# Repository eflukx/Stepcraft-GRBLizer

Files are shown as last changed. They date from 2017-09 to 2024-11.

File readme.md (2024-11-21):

# Stepcraft GRBLizer

A GRBL compatible controller for use as a drop-in replacement for the SC100 USB standard controller deliverd with Stepcraft CNC machines. This Arduino Uno compatible controller is wired conforming the GRL v0.9+ standard. The controller can be used with the GRBL firmware and with EstlCAM.

## Features
  - The PC is fully electrically isolated from the CNC machine (optional).
	- Device is powered via the Stepcraft machine (not from USB port) and optionally from the ISP port.
  - All inputs protected with clamping diodes and resistors.
  - Probe inputs have a 100 Ohm / 10nF low pass filter to suppress spurious triggering. (Filter values may be experimented with.)
  - 3.5mm Jack for spindle / laser / hot-end control
  - 3.5mm Jack input for 2 probes.
  - Serial interface fed out the back (TTL, not protected). For people in a hurry: CP2102 and isolator ICs can be left unpopulated.
  - Standard 6 pin ISP programming connector fed out the back  (not protected).
  - Some juper block for IO-config

Alvast een leuk plaatje:
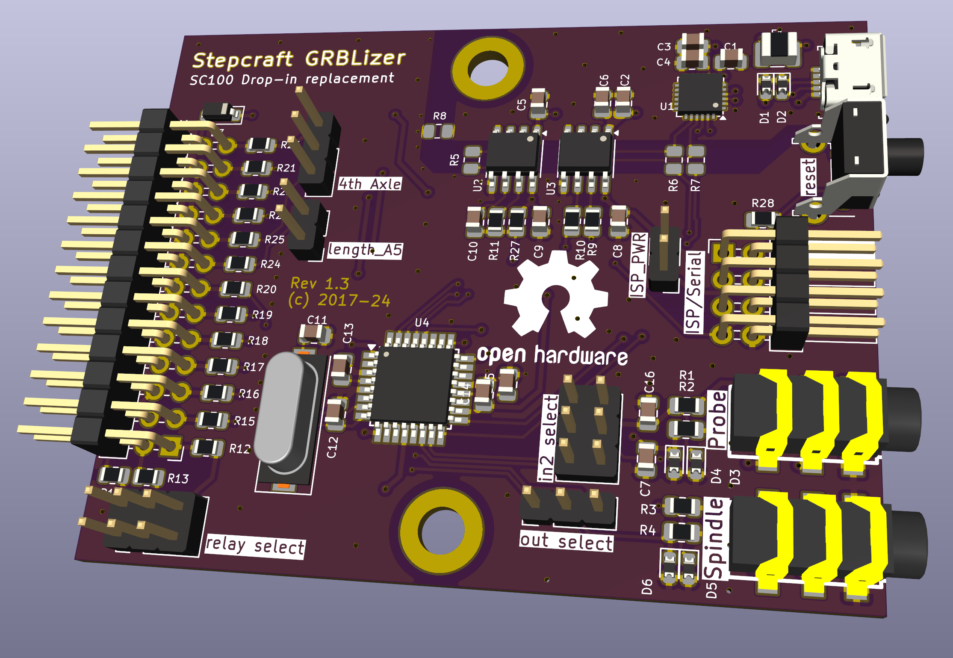
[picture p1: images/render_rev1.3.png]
PCB Render


# interactive BOM
Access the [interactive bom directly using this link](https://cdn.githubraw.com/eflukx/Stepcraft-GRBLizer/4cef8a3f/ibom/ibom.html)!
# Stepcraft 420 CNC settings with GRBLizer

Notes kindly provided by [Albin Stigö](https://github.com/ast) on getting [GRBL v1.1](https://github.com/gnea/grbl/wiki) working with the
[GRBLizer](https://github.com/eflukx/Stepcraft-GRBLizer) board.

Tested on Stepcraft 420, but probably works with most other Stepcraft types.

## Setup

* Stepcraft 420 CNC
* Stepcraft drivers with GRBLizer board
* [GRBL v1.1](https://github.com/gnea/grbl/wiki)
* [Universal-G-Code-Sender](https://github.com/winder/Universal-G-Code-Sender)

Install GRBL in the usual way. However you need to make some changes in config.h and cpu_map.h.

```c
/* cpu_map.h */

// The Stepcraft has all limits on one pin.
#define X_LIMIT_BIT    1  // Uno Digital Pin 9
#define Y_LIMIT_BIT    1  // Uno Digital Pin 9
#define Z_LIMIT_BIT    1  // Uno Digital Pin 9
```

```c
/* config.h */

// Since all limit switches end up being shared on one pin,
// we can only home one direction at a time.
#define HOMING_CYCLE_0 (1<<Z_AXIS)  // REQUIRED: First move Z to clear workspace.
#define HOMING_CYCLE_1 (1<<Y_AXIS)  // OPTIONAL: Then move X,Y at the same time.
#define HOMING_CYCLE_2 (1<<X_AXIS)  // OPTIONAL: Uncomment and add axes mask to enable

// The stop output of the Stepcraft board is inverted to what GRBL expects.
// However you simply can't swap the switch because the driver board will also
// disable the motors so nothing will move.
#define INVERT_CONTROL_PIN_MASK (1<<CONTROL_RESET_BIT) // Default disabled.
```

## GRBL settings

I haven't done a lot of fine tuning but these seems to work well enough.

```
$0 = 50				(Step pulse time, microseconds)
$1 = 100			(Step idle delay, milliseconds)
$2 = 0				(Step pulse invert, mask)
$3 = 0				(Step direction invert, mask)
$4 = 1				(Invert step enable pin, boolean)
$5 = 1				(Invert limit pins, boolean)
$6 = 0				(Invert probe pin, boolean)
$10 = 1				(Status report options, mask)
$11 = 0.010			(Junction deviation, millimeters)
$12 = 0.002			(Arc tolerance, millimeters)
$13 = 0				(Report in inches, boolean)
$20 = 0				(Soft limits enable, boolean)
$21 = 0				(Hard limits enable, boolean)
$22 = 1				(Homing cycle enable, boolean)
$23 = 1				(Homing direction invert, mask)
$24 = 120.000		(Homing locate feed rate, mm/min)
$25 = 900.000		(Homing search seek rate, mm/min)
$26 = 250			(Homing switch debounce delay, milliseconds)
$27 = 1.000			(Homing switch pull-off distance, millimeters)
$30 = 1000			(Maximum spindle speed, RPM)
$31 = 0				(Minimum spindle speed, RPM)
$32 = 0				(Laser-mode enable, boolean)
$100 = 133.333		(X-axis travel resolution, step/mm)
$101 = 133.333		(Y-axis travel resolution, step/mm)
$102 = 133.333		(Z-axis travel resolution, step/mm)
$110 = 800.000		(X-axis maximum rate, mm/min)
$111 = 800.000		(Y-axis maximum rate, mm/min)
$112 = 800.000		(Z-axis maximum rate, mm/min)
$120 = 10.000		(X-axis acceleration, mm/sec^2)
$121 = 10.000		(Y-axis acceleration, mm/sec^2)
$122 = 10.000		(Z-axis acceleration, mm/sec^2)
$130 = 300.000		(X-axis maximum travel, millimeters)
$131 = 420.000		(Y-axis maximum travel, millimeters)
$132 = 140.000		(Z-axis maximum travel, millimeters)
```

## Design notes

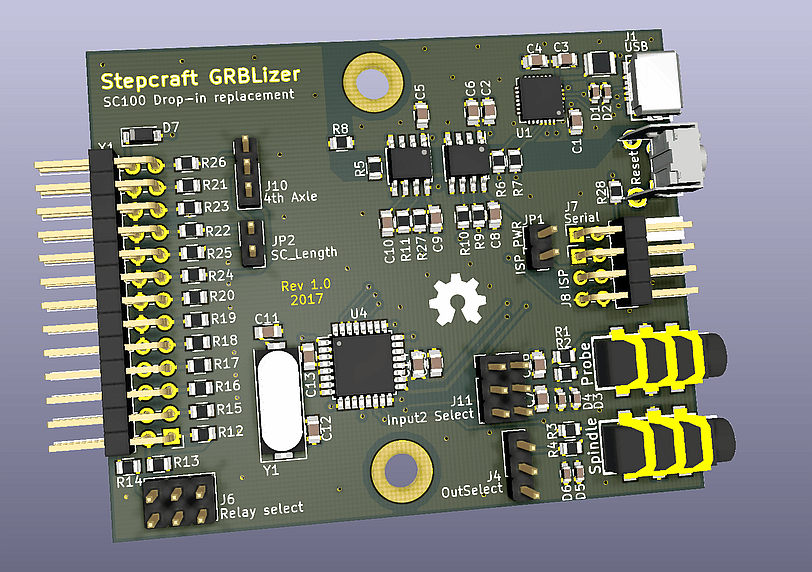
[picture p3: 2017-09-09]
images/render2_composit_web.png

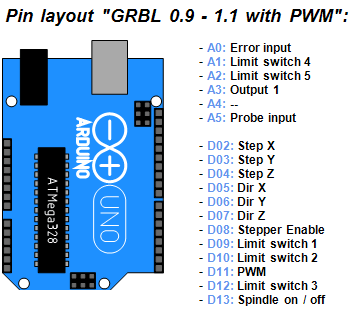
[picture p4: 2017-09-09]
images/GRBL_0.9+_PWM.png

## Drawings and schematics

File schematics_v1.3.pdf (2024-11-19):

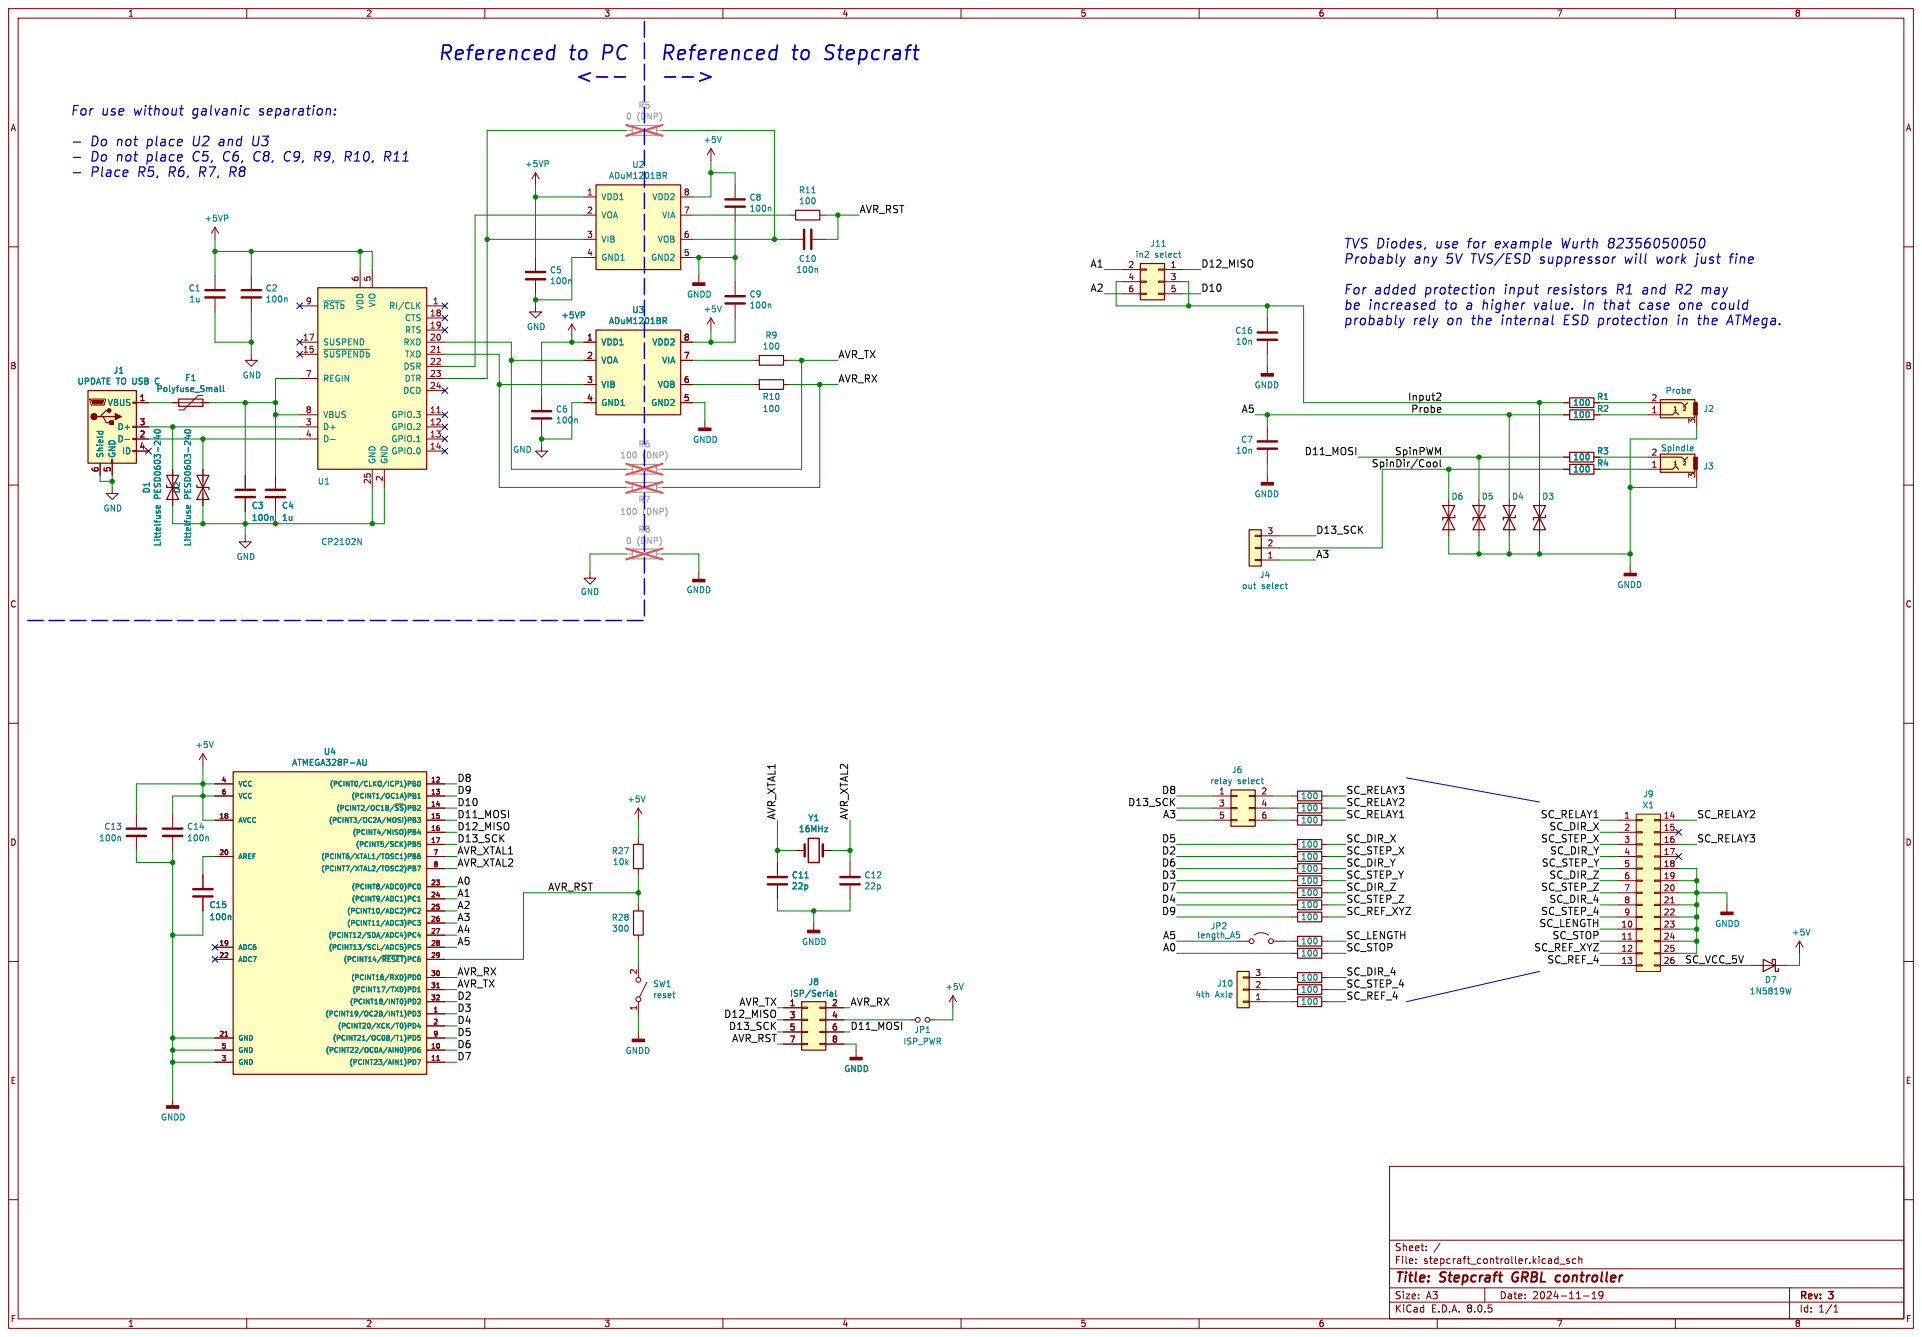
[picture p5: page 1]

TVS Diodes, use for example Wurth 82356050050

be increased to a higher value. In that case one could

2 RXD 20 TXD 21 DSR 22 DTR 23 DCD 24 GND 25 D+ 3 D- 4 VIO

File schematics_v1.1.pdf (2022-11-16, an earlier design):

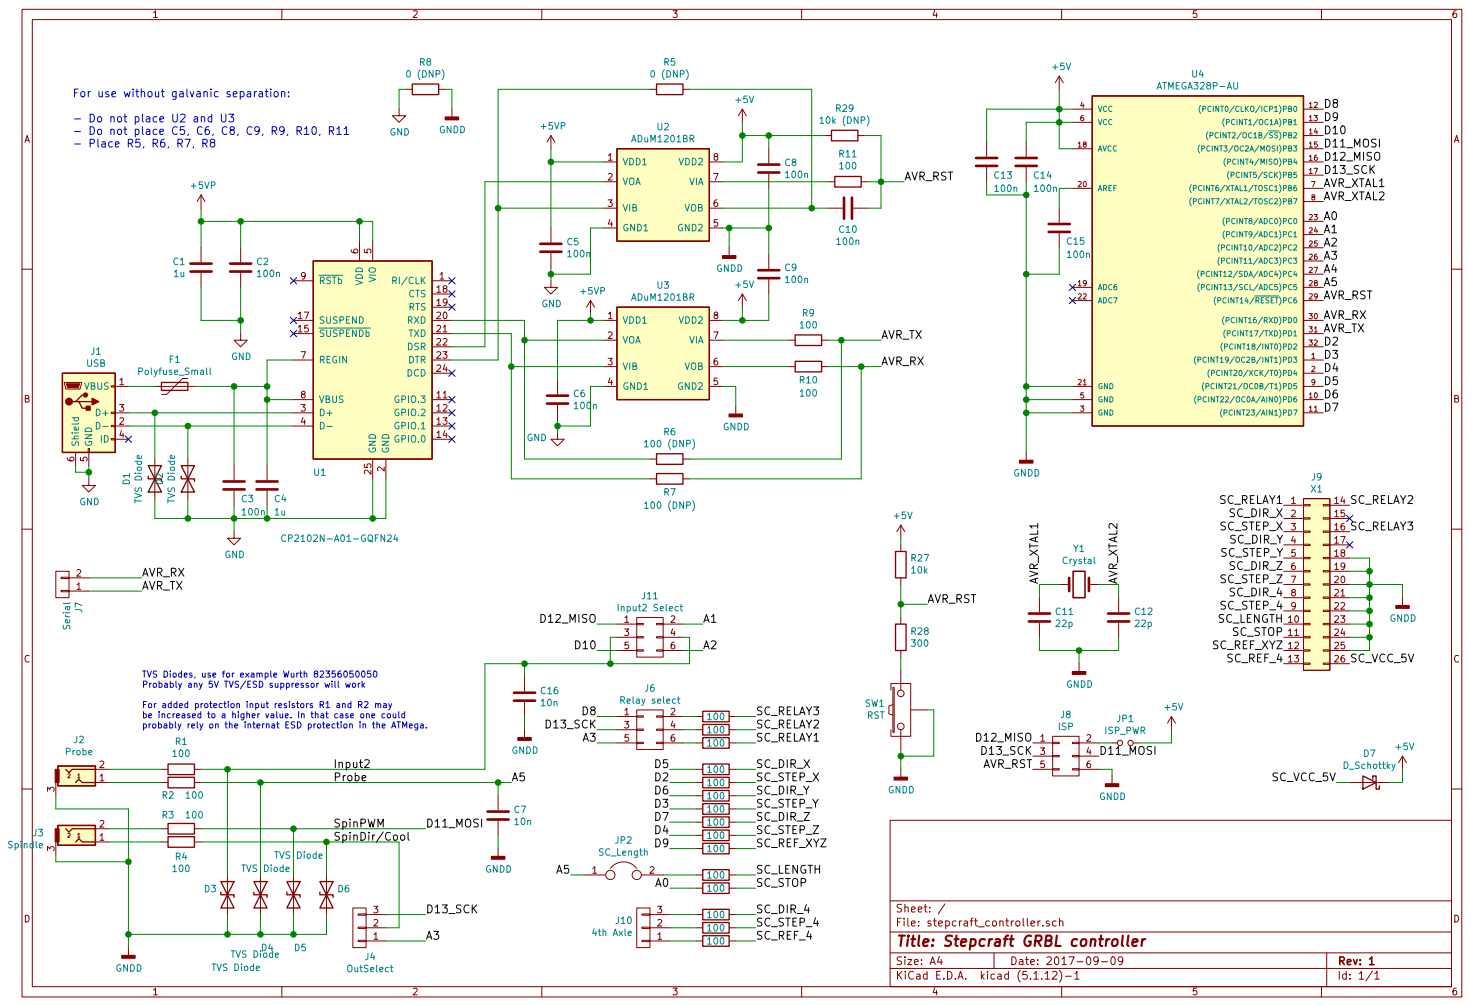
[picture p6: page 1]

For use without galvanic separation:

- Do not place U2 and U3
- Do not place C5, C6, C8, C9, R9, R10, R11
- Place R5, R6, R7, R8

6 REGIN 7 VBUS 8 RSTb 9 U1 CP2102N-A01-GQFN24 GND (PCINT19/OC2B/INT1)PD3 1

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

TVS Diodes, use for example Wurth 82356050050 Probably any 5V TVS/ESD suppressor will work For added protection input resistors R1 and R2 may be increased to a higher value. In that case one could

probably rely on the internat ESD protection in the ATMega.

File: stepcraft_controller.sch Sheet: / D4 TVS Diode

Id: 1/1 Title: Stepcraft GRBL controller

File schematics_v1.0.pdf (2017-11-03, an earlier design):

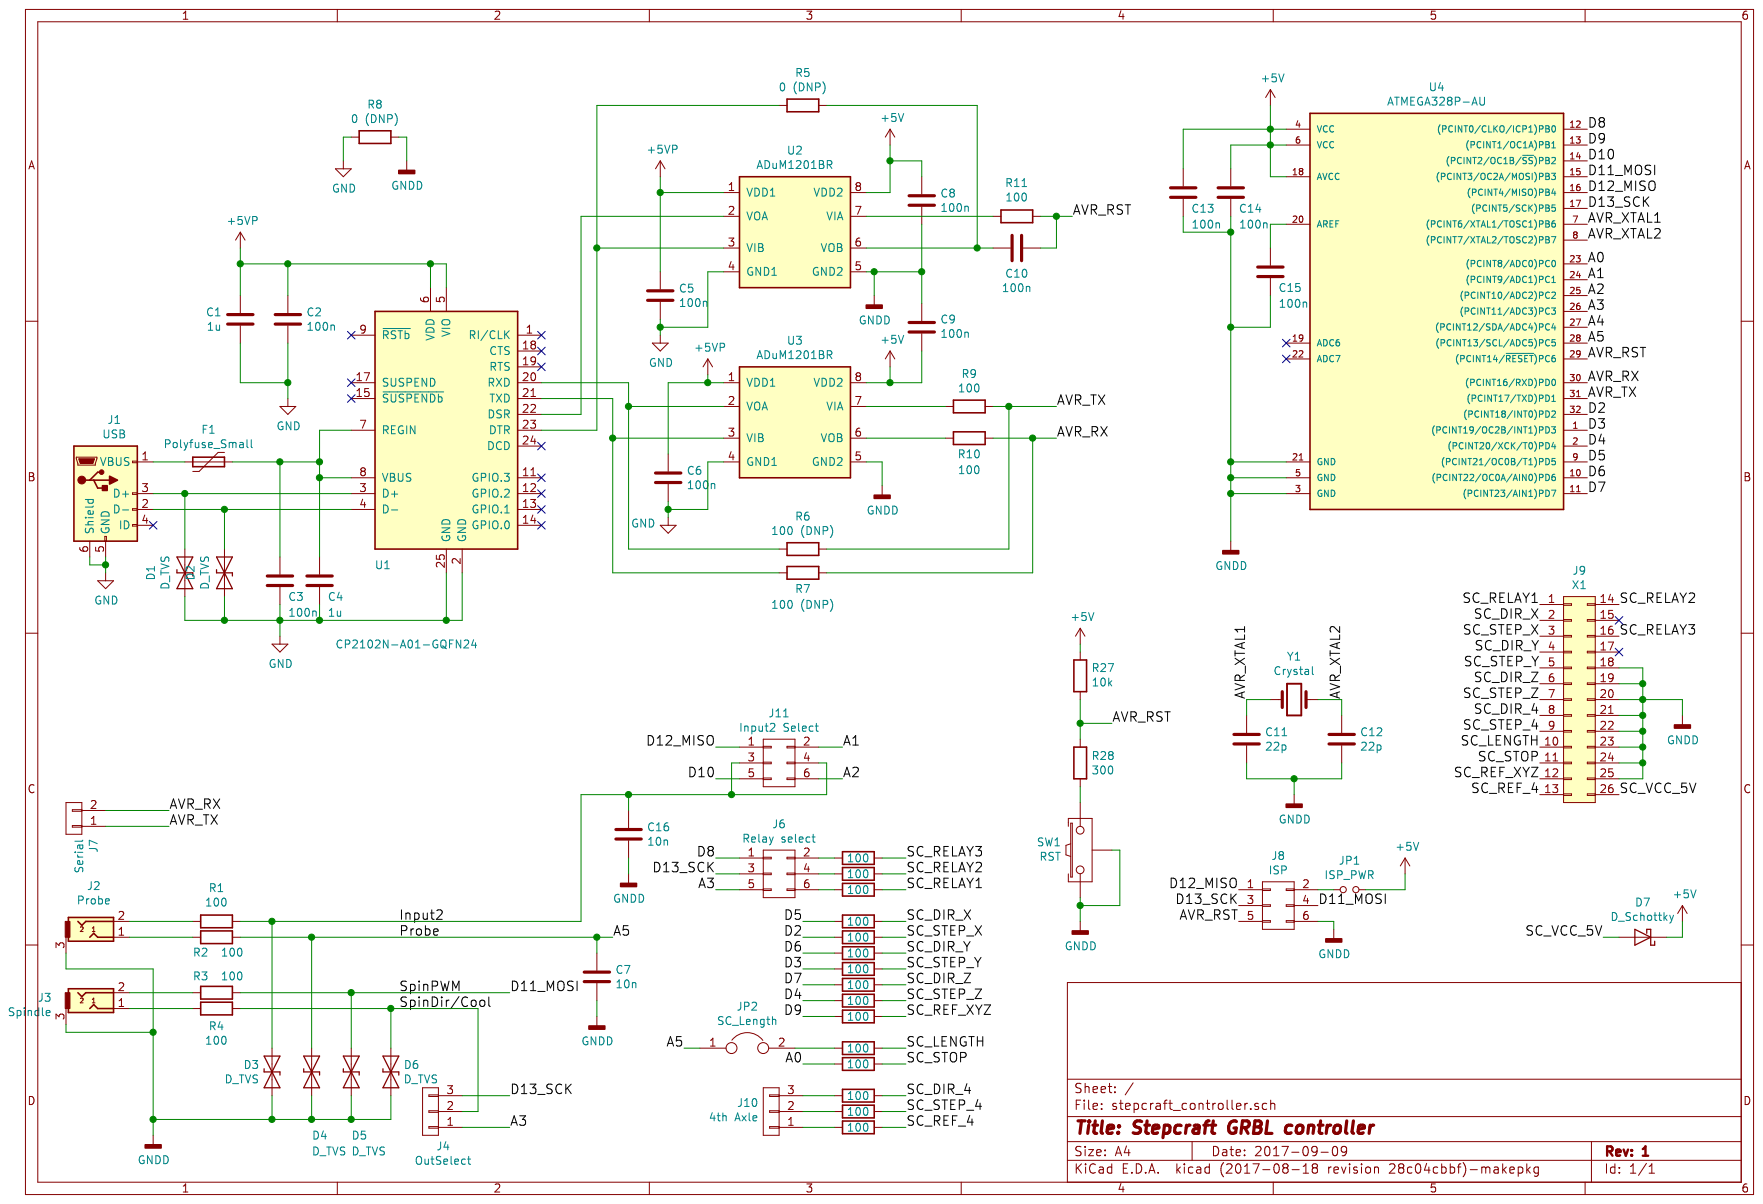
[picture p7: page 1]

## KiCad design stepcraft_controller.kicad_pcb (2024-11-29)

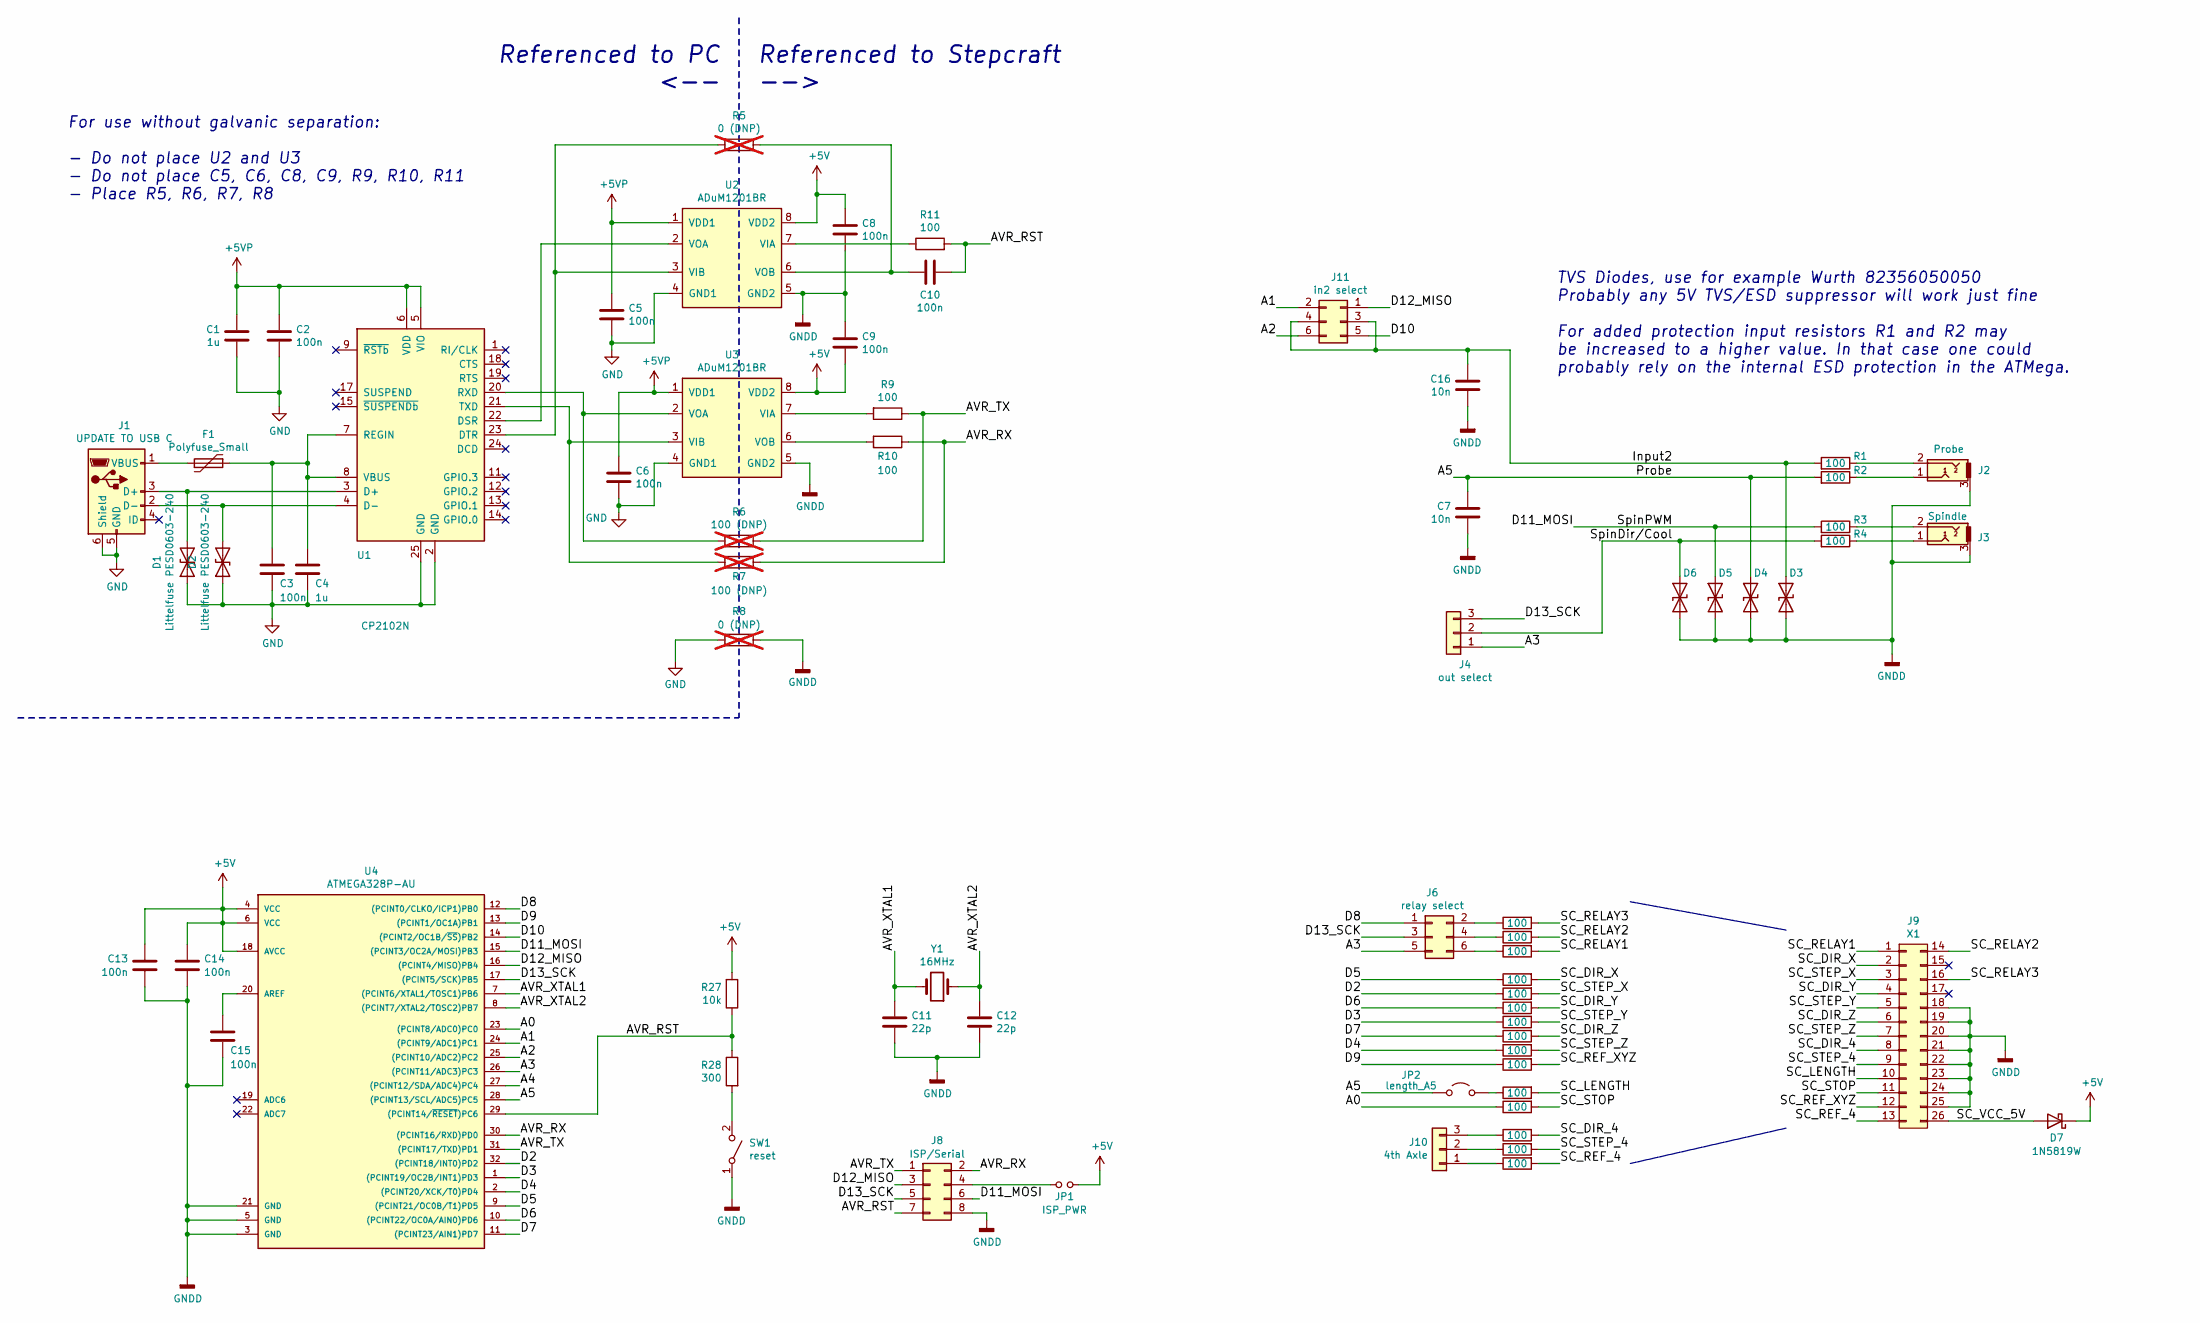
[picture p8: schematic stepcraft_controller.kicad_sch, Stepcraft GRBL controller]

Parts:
C1, C4: 1u; C_0805_2012Metric
C2, C3, C5, C6, C8, C9, C10, C13, C14, C15: 100n; C_0805_2012Metric
C7, C16: 10n; C_0805_2012Metric
C11, C12: 22p; C_0805_2012Metric
D1, D2, D3, D4, D5, D6: Littelfuse PESD0603-240; D_0603_1608Metric; PartNr PESD0603-240; LCSC# C2929617
D7: 1N5819W; D_SOD-123; PartNr 1N5819HW-7-F; LCSC# C82544
F1: Polyfuse_Small; Fuse_1210_3225Metric
J1: UPDATE TO USB C; USB_Micro-B_2_Holes
J2: Probe; jack_3.5_pj313d-smt; PartNr PJ-3135-B; LCSC# C319112
J3: Spindle; jack_3.5_pj313d-smt; PartNr PJ-3135-B; LCSC# C319112
J4: out select; PinHeader_1x03_P2.54mm_Vertical
J6: relay select; PinHeader_2x03_P2.54mm_Vertical
J8: ISP/Serial; PinHeader_2x04_P2.54mm_Horizontal
J9: X1; Stepcraft_SC100_Controller_Board; PartNr Generic connector 2x13pin 2.54mm
J10: 4th Axle; PinHeader_1x03_P2.54mm_Vertical
J11: in2 select; PinHeader_2x03_P2.54mm_Vertical
JP1: ISP_PWR; PinHeader_1x02_P2.54mm_Vertical
JP2: length_A5; PinHeader_1x02_P2.54mm_Vertical
R1, R2, R3, R4, R9, R10, R11, R12, R13, R14, R15, R16, R17, R18, R19, R20, R21, R22, R23, R24, R25, R26: 100; R_0805_2012Metric
R5, R8: 0 (DNP); R_0805_2012Metric; not fitted
R6, R7: 100 (DNP); R_0805_2012Metric; not fitted
R27: 10k; R_0805_2012Metric
R28: 300; R_0805_2012Metric
SW1: reset; SW_Tactile_SPST_Angled_PTS645Vx58-2LFS; PartNr PTS645VJL612LFS; LCSC# C285516
U1: CP2102N; QFN-24-1EP_4x4mm_P0.5mm_EP2.6x2.6mm; PartNr CP2102N-A02-GQFN24; LCSC# C1550551
U2, U3: ADuM1201BR; SOIC-8_3.9x4.9mm_P1.27mm; PartNr ADUM1201BRZ; LCSC# C579376
U4: ATMEGA328P-AU; TQFP-32_7x7mm_P0.8mm; PartNr ATMEGA328P-AU; LCSC# C14877
Y1: 16MHz; Crystal_SMD_HC49-SD; PartNr X49SM16MSD2SC; LCSC# C12676

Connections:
+5V: C8.1, C9.1, C13.1, C14.1, D7.1 (K), JP1.2, R27.2, U2.8 (VDD2), U3.8 (VDD2), U4.4 (VCC), U4.6 (VCC), U4.18 (AVCC)
+5VP: C1.1, C2.1, C5.1, C6.1, U1.5 (VIO), U1.6 (VDD), U2.1 (VDD1), U3.1 (VDD1)
/A0: R23.1, U4.23 ((PCINT8/ADC0)PC0)
/A1: J11.2, U4.24 ((PCINT9/ADC1)PC1)
/A2: J11.6, U4.25 ((PCINT10/ADC2)PC2)
/A3: J4.1, J6.5, U4.26 ((PCINT11/ADC3)PC3)
/A4: U4.27 ((PCINT12/SDA/ADC4)PC4)
/A5: C7.1, D4.1 (A1), JP2.1, R2.2, U4.28 ((PCINT13/SCL/ADC5)PC5)
/AVR_RST: C10.1, J8.7, R11.2, R27.1, R28.1, U4.29 ((PCINT14/~RESET)PC6)
/AVR_RX: J8.2, R7.1, R10.1, U4.30 ((PCINT16/RXD)PD0)
/AVR_TX: J8.1, R6.1, R9.1, U4.31 ((PCINT17/TXD)PD1)
/AVR_XTAL1: C11.1, U4.7 ((PCINT6/XTAL1/TOSC1)PB6), Y1.2
/AVR_XTAL2: C12.1, U4.8 ((PCINT7/XTAL2/TOSC2)PB7), Y1.1
/D2: R16.1, U4.32 ((PCINT18/INT0)PD2)
/D3: R18.1, U4.1 ((PCINT19/OC2B/INT1)PD3)
/D4: R20.1, U4.2 ((PCINT20/XCK/T0)PD4)
/D5: R15.1, U4.9 ((PCINT21/OC0B/T1)PD5)
/D6: R17.1, U4.10 ((PCINT22/OC0A/AIN0)PD6)
/D7: R19.1, U4.11 ((PCINT23/AIN1)PD7)
/D8: J6.1, U4.12 ((PCINT0/CLKO/ICP1)PB0)
/D9: R21.1, U4.13 ((PCINT1/OC1A)PB1)
/D10: J11.5, U4.14 ((PCINT2/OC1B/~SS)PB2)
/D11_MOSI: D5.1 (A1), J8.6, R3.2, U4.15 ((PCINT3/OC2A/MOSI)PB3)
/D12_MISO: J8.3, J11.1, U4.16 ((PCINT4/MISO)PB4)
/D13_SCK: J4.3, J6.3, J8.5, U4.17 ((PCINT5/SCK)PB5)
/Input2: C16.1, D3.1 (A1), J11.3, J11.4, R1.2
/SC_DIR_4: J9.8, R24.2
/SC_DIR_X: J9.2, R15.2
/SC_DIR_Y: J9.4, R17.2
/SC_DIR_Z: J9.6, R19.2
/SC_LENGTH: J9.10, R22.2
/SC_REF_4: J9.13, R26.2
/SC_REF_XYZ: J9.12, R21.2
/SC_RELAY1: J9.1, R12.2
/SC_RELAY2: J9.14 (P2), R13.2
/SC_RELAY3: J9.16, R14.2
/SC_STEP_4: J9.9, R25.2
/SC_STEP_X: J9.3, R16.2
/SC_STEP_Y: J9.5, R18.2
/SC_STEP_Z: J9.7, R20.2
/SC_STOP: J9.11, R23.2
/SC_VCC_5V: D7.2 (A), J9.26
/SpinDir/Cool: D6.1 (A1), J4.2, R4.2
GND: C1.2, C2.2, C3.2, C4.2, C5.2, C6.2, D1.1 (A1), D2.1 (A1), J1.5 (GND), J1.6 (Shield), R8.2, U1.2 (GND), U1.25 (GND), U2.4 (GND1), U3.4 (GND1)
GNDD: C7.2, C8.2, C9.2, C11.2, C12.2, C13.2, C14.2, C15.2, C16.2, D3.2 (A2), D4.2 (A2), D5.2 (A2), D6.2 (A2), J2.3, J3.3, J8.8, J9.18, J9.19, J9.20, J9.21, J9.22, J9.23, J9.24, J9.25, R8.1, SW1.1 (A), U2.5 (GND2), U3.5 (GND2), U4.3 (GND), U4.5 (GND), U4.21 (GND)
unnamed: D1.2 (A2), J1.3 (D+), U1.3 (D+)
unnamed: D2.2 (A2), J1.2 (D-), U1.4 (D-)
unnamed: F1.2, J1.1 (VBUS)
unnamed: J2.1, R2.1
unnamed: J2.2, R1.1
unnamed: J3.1, R4.1
unnamed: J3.2, R3.1
unnamed: J6.2, R14.1
unnamed: J6.4, R13.1
unnamed: J6.6, R12.1
unnamed: J8.4, JP1.1
unnamed: J10.1, R26.1
unnamed: J10.2, R25.1
unnamed: J10.3, R24.1
unnamed: JP2.2, R22.1
unnamed: R28.2, SW1.2 (B)
unnamed: U1.22 (DSR), U2.2 (VOA)
unnamed: R5.2, U1.23 (DTR), U2.3 (VIB)
unnamed: C3.1, C4.1, F1.1, U1.7 (REGIN), U1.8 (VBUS)
unnamed: R6.2, U1.20 (RXD), U3.2 (VOA)
unnamed: R7.2, U1.21 (TXD), U3.3 (VIB)
unnamed: R11.1, U2.7 (VIA)
unnamed: C10.2, R5.1, U2.6 (VOB)
unnamed: R9.2, U3.7 (VIA)
unnamed: R10.2, U3.6 (VOB)
unnamed: C15.1, U4.20 (AREF)

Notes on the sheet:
TVS Diodes, use for example Wurth 82356050050 Probably any 5V TVS/ESD suppressor will work just fine For added protection input resistors R1 and R2 may be increased to a higher value. In that case one could probably rely on the internal ESD protection in the ATMega.
Referenced to Stepcraft -->
Referenced to PC <--
For use without galvanic separation: - Do not place U2 and U3 - Do not place C5, C6, C8, C9, R9, R10, R11 - Place R5, R6, R7, R8

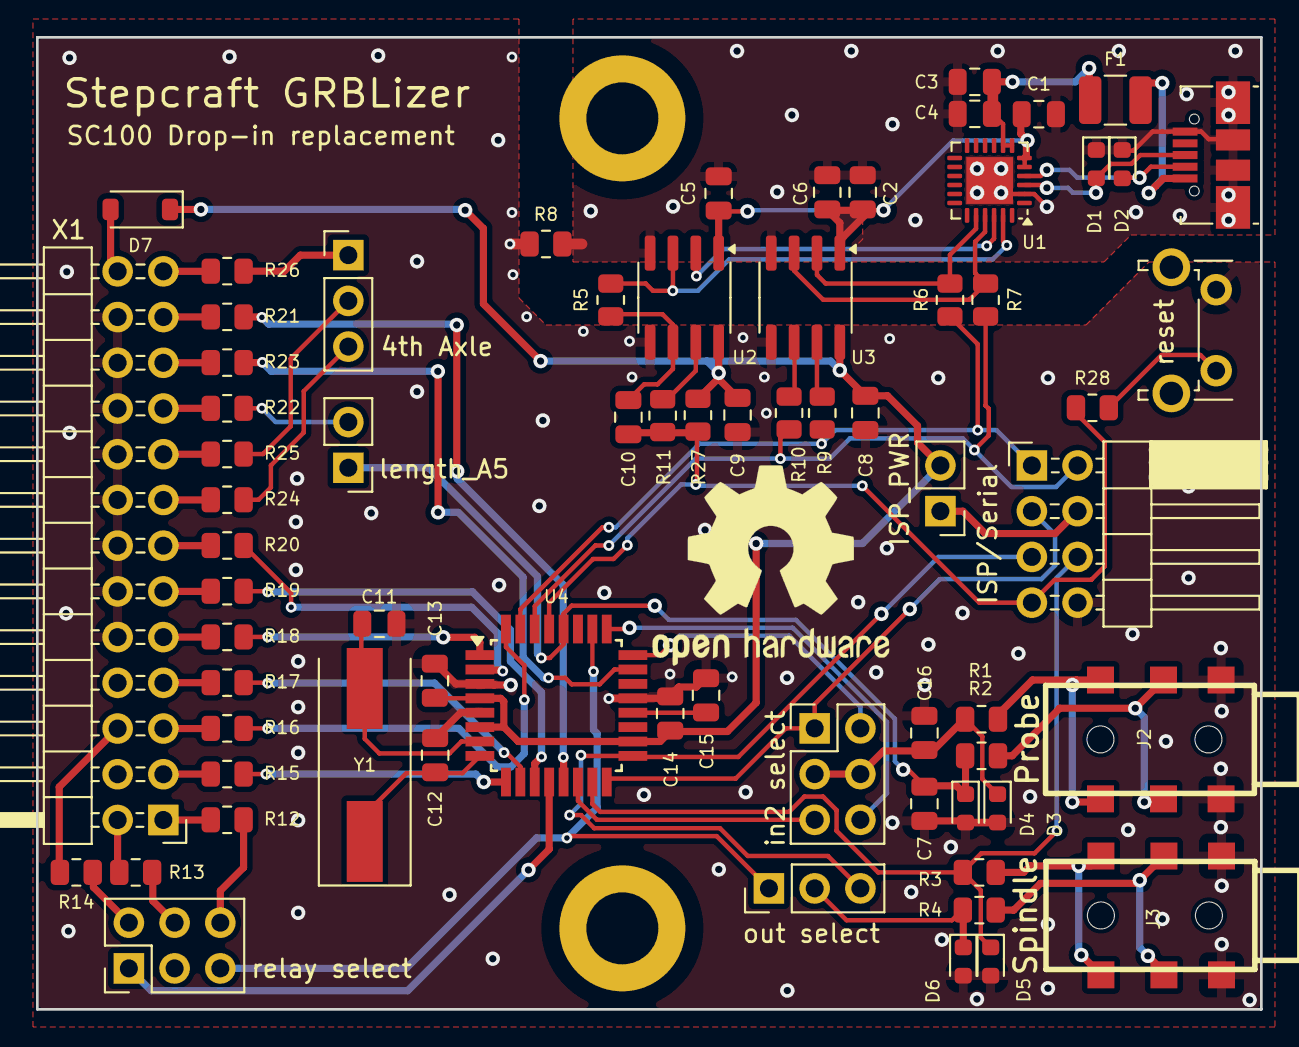
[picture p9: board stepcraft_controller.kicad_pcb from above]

Board: 2 copper layers, 68.0 x 54.0 mm, 69 parts (0 on the bottom side), 70 nets.

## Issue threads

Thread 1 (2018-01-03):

Link to more info?

ast, 2018-01-03:
Can I purchase this somewhere?

Would be great with a link to more info!

eflukx, 2018-01-03:
Hi,

Thanks for your interest in this. I do have some (vague) plans to get 50-100 produced of these and sell those online.

Currently I have (hand)built a few of those, but I have only one Stepcraft 840.. :) Happy to ship one to you @cost price. I also have some bare PCB's left, in case you're interested. Consider yourself a "beta tester": I'm open for improvements for a final version.

Ps. these are "v1" units with some "bugs", mostly swapped pinning of the jacks.

ast, 2018-01-03:
I have a Stepcraft 420.

I have their motor driver PCB and USB "adapter" but never used it, so it would be great if I could use your GRBLizer with the stepcraft motor driver. It would also tidy things up a bit :-)

I currently use an Arduino with CNC shield R3 (DRV8825 drivers) and GRBL (and some hand wiring to the limit switches).

I'd be happy to betatest this for you.

I'm keeping some notes of my setup here:
http://albinstigo.me/post/stepcraft/

Email me at albin.stigo@gmail.com and lets work something out!

eflukx, 2018-01-03:
Yep I started off with the standard SC100 USB controller as well (was looking for something that just worked...). But I was _really_ disappointed with the WinPC software delivered with it (I even paid the >200,-- license for it). Also disappointed in the Stepcraft company that they deliver a product aimed for the DIY/hobby/makers market that is based on a fully closed/opaque USB controller. (IMO this harms the value of their product, delivering GRBL or something more open would make very much sense!)

Anyway, give the GRBL firmware a try (nice project!) but needed hardware that nicely fits the Stepcraft.

_Will contact you via email to exchange details._

eflukx, 2018-02-04:
Oh.. in case someone's interested I have some of the v1 units lying around here..

Closed 2018-02-04.

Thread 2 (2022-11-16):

BOM details

Pixelbrick, 2022-11-16:
Hi,

Thanks very much for sharing this. I work as a technician in a university makerspace & we're looking to put together a few of these boards for the routers we have here.

Could you let us know which TVS suppression diodes & poly-fuse you recommend please? Other stuff we can easily swap out for what we can get/have on hand.

Cheers,
Jay

eflukx, 2022-11-16:
Ha.. it has been a loong time since I touched this project.. 😄  (I'm still using my first version in my Stepcraft 840 :))
One thing i recalled that there was a problem in the footprint of the aux TRS connectors.. (pins 3 and 1 swapped), so the `gnd` is connected to the `R`ing of the TRS connector in stead of the `S`leeve. Allow me to update the board for you! :)

About those (TVS) diodes, I don't think these are too critical, but I will include a type nr in the BOM.

Pixelbrick, 2022-11-16:
Oh wow!

I didn't expect a response, let alone an incredibly helpful one in minutes :)

Cheers,
Jay

eflukx, 2022-11-16:
I fixed the pinning issue with the output jacks and made some remarks on the schematic. Also made some changes (improvements hopefully) to the routing.
(This is was a Kicad 4 project, made the updates using Kicad 5, but should work fine now in v6 as well)

Pixelbrick, 2022-11-23:
That's brilliant.

Much appreciated,
Jay

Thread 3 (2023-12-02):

Add KiCAD Libraries to Project

JulKramer3G, 2023-12-02:
Hi There,
I really like your board and I would like to adapt it to the newer Series 3 Stepcraft machines.
Unfortunately the KiCAD project you provided uses **libraries** linked to **local paths on your computer**.
Could you provide the used libraries (.lib or similar) to the project and upload them to GitHub?
I added a screenshot of what the design looks like on a different computer.
Thank you very much and have a nice day!
Greetings from Germany!
Julius
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

JulKramer3G, 2023-12-02:
The following libraries are mentioned in the KiCAD project (file sym_lib_table):
(sym_lib_table
  (lib (name stepcraft_controller-rescue)(type Legacy)(uri ${KIPRJMOD}/stepcraft_controller-rescue.lib)(options "")(descr ""))
  (lib (name iotta_wsn_rev2)(type Legacy)(uri C:/code/Hardware/iotta-kicad-libs/iotta_wsn_rev2.lib)(options "")(descr ""))
  (lib (name w_connectors)(type Legacy)(uri C:/code/Hardware/iotta-kicad-libs/smisioto.no-ip.org/w_connectors.lib)(options "")(descr ""))
)

eflukx, 2024-11-19:
Somehow I wasn't notified this issue was open 😨... I'm not sure if this is still relevant to you, sorry about that. Anyway, I will update this project to KiCad 8 and export including all syms shortly!

Closed 2024-11-19.

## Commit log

2017-09-09 Add schematics and (unrouted) board
    [stepcraft_controller.kicad_pcb, stepcraft_controller.sch]
2017-09-09 Update schematics and board, fully routed board
    [stepcraft_controller.kicad_pcb, stepcraft_controller.sch]
2017-09-09 Update PCB routing.
    [stepcraft_controller.kicad_pcb, stepcraft_controller.sch]
2017-09-11 Fix net name (D13), improved routing, ground plane continuity.
    [stepcraft_controller.kicad_pcb, stepcraft_controller.sch]
2017-09-20 Change SiLabs CP2102 QFN-28 to (more common) CP2102N QFN-24
    [stepcraft_controller.kicad_pcb, stepcraft_controller.sch]
2017-09-20 Update Schematics.pdf to include changes in 855a5c1
2017-11-03 Fix Diode symbol (was reversed), input dcouple caps value, X1 caps value, minor routing improvement.
    [stepcraft_controller.kicad_pcb, stepcraft_controller.sch]
2018-07-02 Add Albin's notes on GRBL firmware on SC machines
2022-11-16 Update to Kicad 5, add remarks about galvanic isolation
    [stepcraft_controller.sch]
2022-11-16 Fix TRS jack pinning Improve some of the scuffy routing...
    [stepcraft_controller.kicad_pcb]
2022-11-16 Some more minor routing improvements
    [stepcraft_controller.kicad_pcb]
2022-11-16 Add schematics PDF for Rev 1.1 (`schematics_v1.1.pdf`)
2024-11-19 Update project to KiCad v8
    - remove all references to external footprints/symbols (close issue #3)
    - update footprints to new standard footprint
    - add components mgf partnos and LCSC part# for all non standard parts
    - shrink PCB outline by 2x0.25mm (for a better fit in machine)
    - improve routing
    [stepcraft_controller.kicad_pcb, stepcraft_controller.kicad_sch, stepcraft_controller.sch]
2024-11-21 Add interactive BOM for hand-placing parts
2024-11-29 Some silkscreen designator placement improvements
    [stepcraft_controller.kicad_pcb]

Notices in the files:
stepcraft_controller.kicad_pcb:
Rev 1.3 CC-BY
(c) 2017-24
